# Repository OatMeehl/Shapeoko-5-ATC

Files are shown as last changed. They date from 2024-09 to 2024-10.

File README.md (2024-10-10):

# Shapeoko 5 Pro 4x4 ATC
Shapeoko_5_Pro_Machine Render
Tool Print+Render

### Things needed to buy;

2.2kw water cooled spindle with VFD - https://www.aliexpress.us/item/3256802808501425.html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

80mm Spindle Mount - I machined my own but it looks like Carbide3D has one now. https://shop.carbide3d.com/products/80mm-spindle-mount-s5

Cooling System - either a tank of water with a submersible pump or a small chiller.

Air compressor - The quiet ones are nice - https://www.harborfreight.com/1-gallon-135-psi-ultra-quiet-oil-free-hand-carry-jobsite-air-compressor-64592.html

Enclosure - 12x16x8 (400x300x200mm) https://www.aliexpress.us/item/3256802803514635.html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

Air Pump - Creates constant positive pressure to keep dust out of spindle bearings. https://a.co/d/5YxAlrj

(Qty 7) - Proximity Sensors - https://a.co/d/2bBb0iI

ISO20 Tool Holders - https://a.co/d/e9mtsC4

Timer Relay - https://a.co/d/9uUspSC

24V Power Supply - https://a.co/d/etT1WPE

Solenoid Valve - https://a.co/d/fbD1gJ7

Tool Release Button - https://a.co/d/0YxQrxa

PG13.5 Cable Glands - https://a.co/d/78sGWZN

6mm Flow Control - https://a.co/d/1PORBhs

6mm Y Splitter - https://a.co/d/9BAZi52

Terminal Block - https://a.co/d/eLBwwW1

(Qty 14) M6 Nuts - https://a.co/d/6r6Xlbk or just go to your local hardware store

(Qty 14) M6x14 SHCS - https://a.co/d/dRKVwIe or just go to your local hardware store

This is a fairly involved project to take on. The requirement to install a 220V circuit for the spindle and do the wiring and VFD setup might be a bit much for some people. If you have some solid mechanical and electrical skills you should be good to go. I'll show what I did as much as I can but I'm sure I'll be missing some stuff since I did most of this over a year ago. Use common sense and build at your own risk!

***This will only work if you are using the Fusion360 payed version since the free one doesn't allow tool changes. If Carbide3D would open up their Carbide Create posts for editing I could maybe add the Gcode that would be needed to make this work, but currently that isn't the case. Even if you don't use automated tool changing, the convenience and speed of manual tool changes is still worth it in my opinion.

This is a project for an automated tool changing system for the Shapeoko 5 Pro CNC router without having to upgrade the machine controller and retaining the use of Carbide Motion software. It uses an Aliexpress ATC spindle and other components to make it happen. The tool pocket stations mount directly to the table. The tool changes are controlled by G code output from a Fusion 360 Post processor. When the spindle goes to a tool location and gets within range of the proximity sensor, the tool release solenoid is activated and is latched in by a timer relay with a 3 second latch time. During that time the spindle will fully lower into the tool position. To pick up a tool the spindle needs to stay in the position longer than the timer relay time and to drop off a tool it needs to leave before that time. The G code then issues an M6 which will cause Carbide Motion to give a confirmation dialog. I use Dialog Demon https://dair.com/ddevil/ to auto-confirm that dialog. Then our tool measure cycle can commence and we're ready to party! 

## Video Demo doing 4 tool changes here;

HERE (https://www.youtube.com/watch?v=65O__KrGo3E)

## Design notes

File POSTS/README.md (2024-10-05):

## FUSION 360 Post Processor

I have only tested this in Inch mode. In theory it should also work in Metric, but use caution!

**Adjust post for your tool pocket locations.**

All positions are in Machine Coordinates.



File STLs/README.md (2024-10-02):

Print "Tool Holder ISO20" with ABS for flexability and strength with enough walls to make them solid through the bendy part.

The "Tool Release Button Enclosure body" has the tool release text debossed into it very slightly. If you have a multi-color 3D printer you can paint that debossed surface to get that text to show up.
Tool Release Render

The "T-Slot with M6 Nut" is meant to have an M6 nut encased inside the print. Set a pause just below the layers that would cover the nut and insert the nuts during the pause.

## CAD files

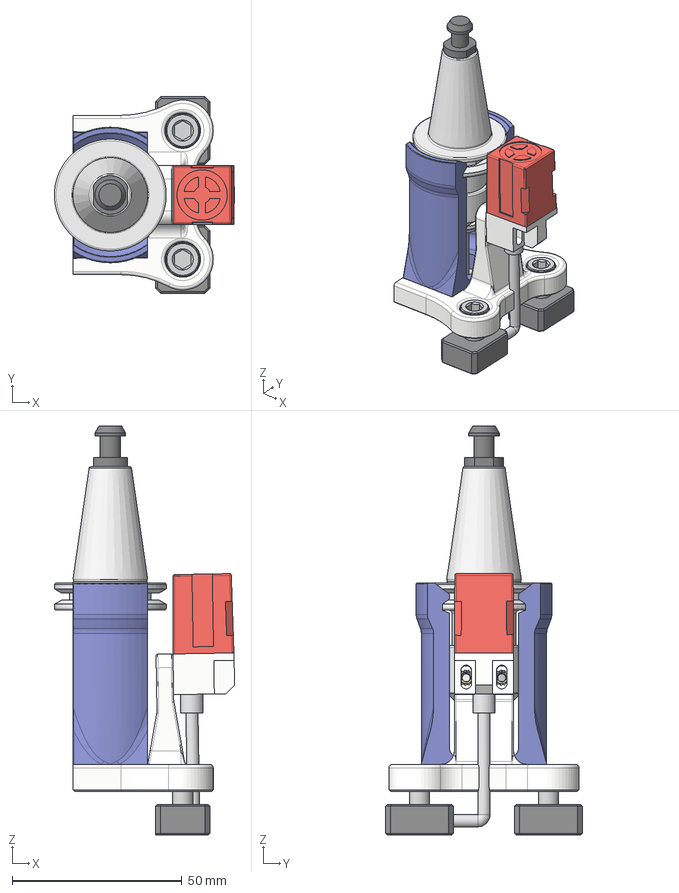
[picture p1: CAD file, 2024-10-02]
CAD/ISO20 Tool Holder Shapeoko 5 Pro.step
53.1 x 58.0 x 120.6 mm
Pull Stud
ER16 Nut
Probe Pin
PL-08N Proximity Sensor
Latch B Base
Latch Removable Clip
94459A130_Heat-Set Inserts for Plastic x 2
Tees Nut M6
90592A016_NO THREADS_Steel Hex Nut
91290A318_NO THREADS_Alloy Steel Socket Head Screw x 2

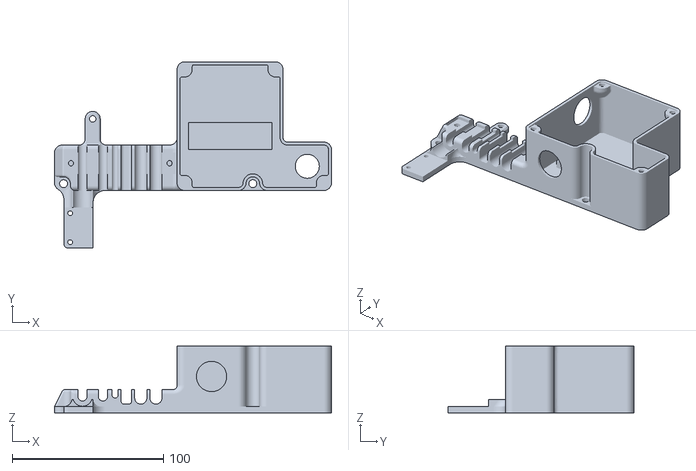
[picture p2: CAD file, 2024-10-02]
STLs/Tool Release Button Enclosure Body.stl
183.0 x 123.1 x 44.0

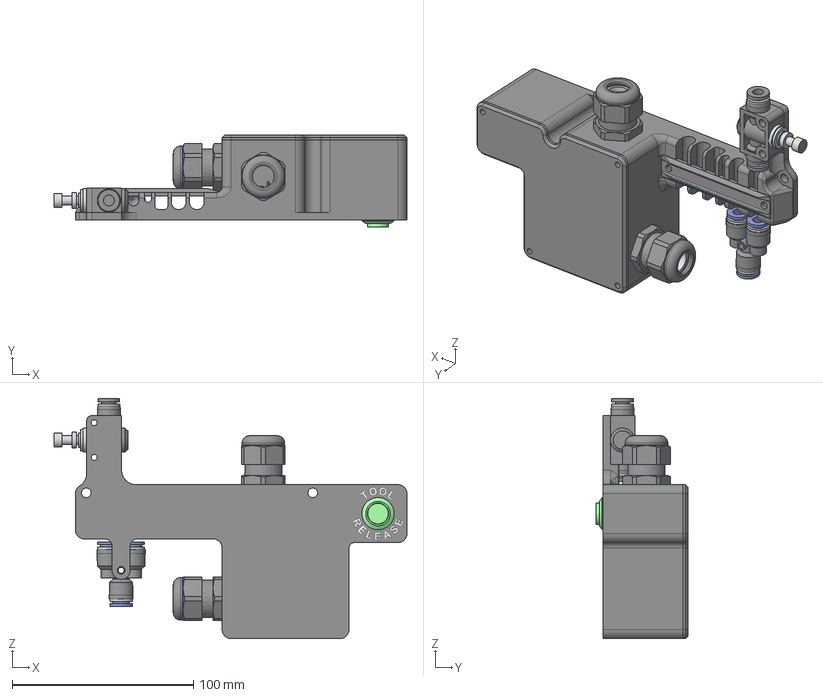
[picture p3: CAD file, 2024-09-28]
CAD/Tool Release Button Enclosure.step
194.8 x 51.0 x 132.6 mm
Cable Cover
7527K44_300V AC 300V DC Terminal Block
69915K13_NO THREADS_Plastic Submersible Cord Grip x 2
6mm Flow Control
Tool Release Button
Enclosure Lid
6mm Y Splitter

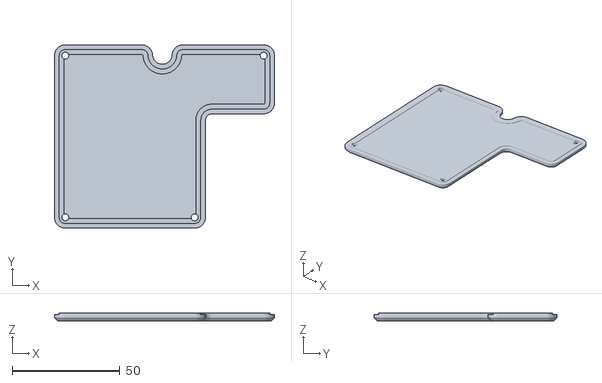
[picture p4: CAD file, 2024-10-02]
STLs/Tool Release Enclosure Cover.stl
102.0 x 85.0 x 3.50

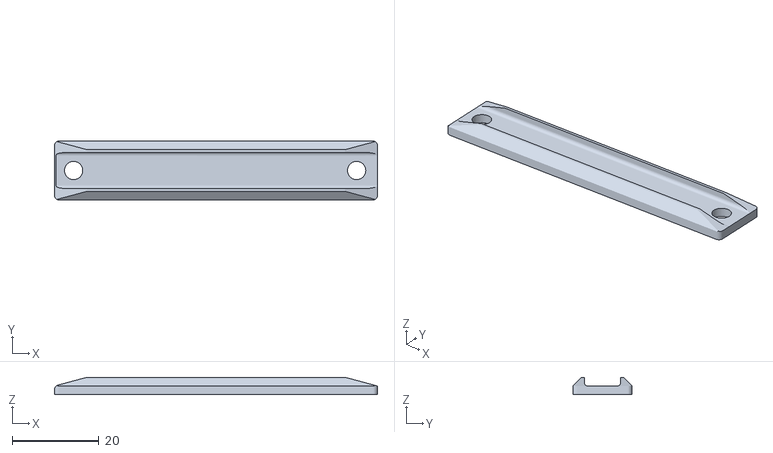
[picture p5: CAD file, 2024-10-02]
STLs/Tool Release Cable strap.stl
74.3 x 13.6 x 4.00

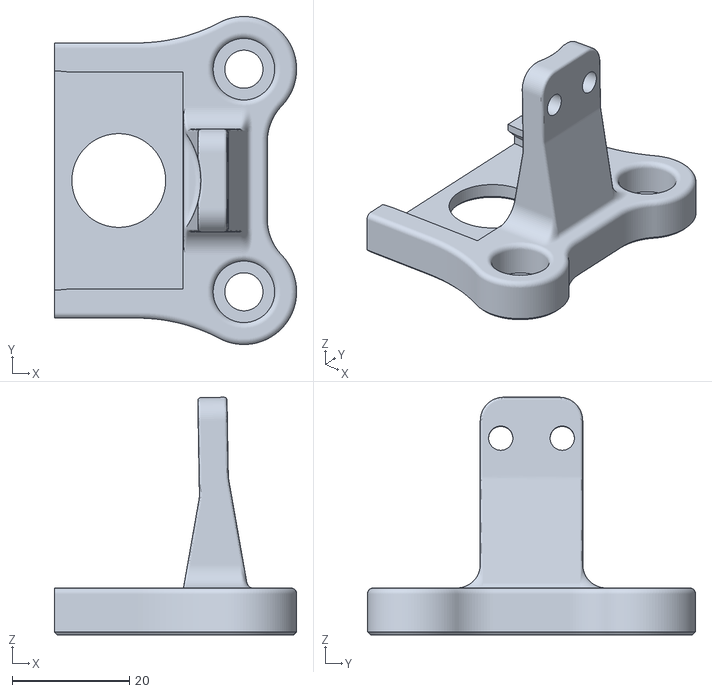
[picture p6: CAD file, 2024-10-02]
STLs/Tool Holder Dovetail Base.stl
41.4 x 56.0 x 40.6

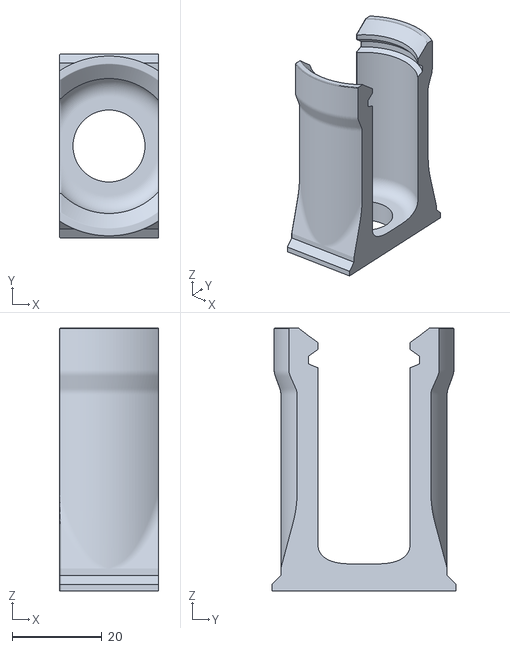
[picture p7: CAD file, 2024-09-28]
STLs/Tool Holder ISO20.stl
22.0 x 41.0 x 58.5

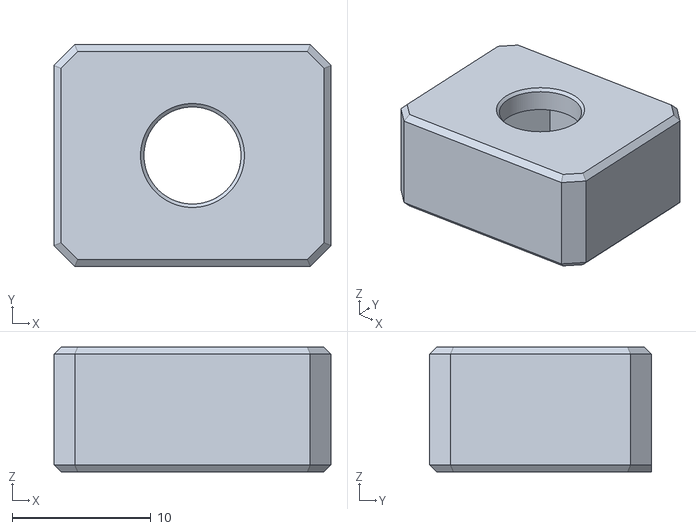
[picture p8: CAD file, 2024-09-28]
STLs/T-Slot with M6 Nut.stl
20.0 x 16.0 x 9.00

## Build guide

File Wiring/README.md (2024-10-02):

# Wiring / Electronics
The wiring is based around the VFD, the proximity sensors, and the solenoid valve. The VFD gets the analog signal from the Shapeoko controller. That is what turns the spindle on and sets the speed. For safety I wired the tool release solenoid valve through the VFDs relay output with the parameter defined to be closed any time the spindle is spinning. That prevents the tool from being released at speed, which would be a disaster. I'm going to put together an enclosure layout and wiring diagram for all this.
